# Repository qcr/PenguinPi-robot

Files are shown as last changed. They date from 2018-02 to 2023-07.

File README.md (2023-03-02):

PenguinPi Robot
===============

# Synopsis

This site describes an open-source low-cost robot for educational purposes: hardware and software.

PenguinPi robot

The robot is used for teaching mobile robotics, robotic vision within QUT's EGB439 Advanced Robotics unit.

Key features of the robot are:

* low cost, less than AUD 500
* Raspberry Pi 3B computer with a color camera
* an i/o board with embedded processor that interfaces with motors and provides a simple UI (20x4 OLED display, 4xpushbuttons and various other LEDs)
* a MATLAB-based API, MATLAB code running on a host computer communicates over WiFi with a server running on the robot
* ability to run code onboard written in Python or C++

Example of MATLAB API usage:
```matlab
robot = PiBot('192.168.3.4')
robot.setVelocity(20, -20); % set left & right wheel speeds to +20 and -20 respectively
robot.stop(); % stop the robot moving
batteryVoltage = pb.getVoltage(); % get battery voltage
pb.setLed(2, true);  % turn on the green LED
pb.printfOLED('hello world'); % write string to the OLED display
im = pb.getImage(); % get RGB image from the camera
```

PenguinPi robot

# Mechanical design

The robot has two independently controllable wheels driven by geared DC brushmotors, and a single castor.  The frame is built from laser cut acrylic.

An [animation of the assembly](https://youtu.be/HddVRaQIhIY).

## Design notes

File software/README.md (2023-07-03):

# Welcome to EGB439 Advanced Robotics
Included in this repository is the Python, MATLAB and C code used to operate the PenguinPi using the Raspbian Bullseye (64-bit) operating system.

## Folder structure
The main folders are:
  - [python/robot](./python/robot) Python server that runs on the Raspberry Pi and accepts web service requests. There should be no need to touch this for you.
  - [matlab](./matlab) runs on your computer and talks to the Python server running on the robot.
  - [python/client](./python/client) is an unsupported alternative to the MATLAB client.
  - [atmelStudio](./atmelStudio) C code that runs on the Atmel processor (on the i/o board) that connects the Pi to the robot hardware. There should be no need to touch this for you.

## Startup scripts
The scripts that automatically launch on the robot when starting up are:
* [ppweb.py](./python/robot/ppweb.py) - this is the webserver that MATLAB communicates with.
* [GPIOSoftShutdown.py](./python/GPIOSoftShutdown.py) - this allows you to safely shut down the PenguinPi by means of pressing a button.

## Raspberry pi login
* Username: `pi`
* Password: `PenguinPi` - see [instruction to change](https://www.raspberrypi.com/documentation/computers/configuration.html#change-the-default-password)
* You may want to [change your hostname](https://www.howtogeek.com/167195/how-to-change-your-raspberry-pi-or-other-linux-devices-hostname/). If you wish to change this please speak to your tutor.

## Connecting to your Pi
### The easy way
The easiest way is to connect via a screen and keyboard/mouse. 

### Via Wifi
You can also connect to the PI over the network using ssh over WiFi or the Ethernet cable. See the [README-WiFi.md](README-WiFi.md).

### Using an ethernet cable
The ethernet port can be used. It will be assigned an IP address from the DHCP server in your network (e.g. of the QUT DHCP server). The IP will be shown on the Pi's screen.

### Internet access for the PenguinPi using the QUT Enterprise Network
If you can connect to your PenguinPi on the QUT network, but cannot access internet, you have to use the IAClient. You can set it up by using `~/InternetAccessClient_Linux_ARM32v71-RaspberryPi_v4.0.250_QUT/IAClientConfigCmd` and entering your username and password. If the domain is empty, please enter `qut.edu.au`. You can then run `~/InternetAccessClient_Linux_ARM32v71-RaspberryPi_v4.0.250_QUT/IAClient` in a terminal and keep it open (or run in the background by appending ` &` after the command).

### Old instructions, please ignore or use with caution
<details><summary>More details, but use with caution!</summary>
If you need the IP address to stay the same, it is highly recommended you don't use a static IP, but try using a hostname. If you still must have a static IP address, do not edit the `/etc/network/interfaces` file. Since Raspian Jessie, you should use the `/etc/dhcpcd.conf` file to set a static IP address; to do so, follow these [instructions](https://raspberrypi.stackexchange.com/questions/37920/how-do-i-set-up-networking-wifi-static-ip-address/74428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) or [these ones](https://www.tomshardware.com/how-to/static-ip-raspberry-pi).

If you want to access the internet over the PenguinPis WiFi hotspot (using the raspberry pi as a WiFi router), you will have to enable IP forwarding. This is already enabled by default.
</details>

## Deploying a PenguinPi
- Flash the HAT: `cd ~/PenguinPi-robot/software/atmelStudio && make` (Steven Bulmer to update instructions)
- Set up the network with the correct MAC for the robot: `cd ~/PenguinPi-robot/software/scripts && sudo sh update_networking_script.sh`
- Reboot the PenguinPi
- Set up the proxy: `cd ~/PenguinPi-robot/software/scripts && sh setup_proxy.sh`
- On your local machine, run the `motortest.m` and `cameratest.m` scripts (MATLAB) or the `test_camera_motors.py` script (Python). Note that you will need to update the IP - for the Python script, simply run `python test_camera_motors.py --ip AAA.BBB.CCC.DDD`.

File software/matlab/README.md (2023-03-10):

# MATLAB interface to PenguinPi

The code here allows you to control the robot and access its camera from the MATLAB environment.  You need to have the file
```PiBot.m``` in the current directory or on your MATLAB path.  The Raspberry Pi needs to be running the Python server code [ppweb.py](../python/robot/ppweb.py) (this happens automatically at startup).

## Establishing a connection
We start by connecting to the remote Raspberry Pi
```
pb = PiBot('192.168.1.141');
```
which requires the IP address of the RPi on the network.  This might be the one assigned by the WiFi access point in the 
lab or a hardwired address 192.168.0.100 for the wired ethernet port. 
The result is an object that is a connector to the remote RPi.

## Obtaining camera images
To obtain an image is simply
```
img = pb.getImageFromCamera();
```
which is an RGB image with uint8 pixel data.  Typically acquiring an images takes 100-200ms.

### IP camera package
To obtain images, you need the [MATLAB Support Package for IP Cameras](https://au.mathworks.com/help/supportpkg/ipcamera/index.html). Typically installation is straightforward - MATLAB will simply ask you to install the package when you try to use the `ipcam()` function and you do not have the support package installed. In case you get errors that "There was a problem downloading the support package", please use the [Download Support Packages](https://au.mathworks.com/support/install/support-software-downloader.html) application on a different machine and follow the instructions.

## Motor control
### Access the motor encoders
```
ticks = pb.getMotorTicks();
```
which returns a 2-vector containing the integer tick counts for motor A and motor B.  These are in units of degrees of wheel rotation and wrap around at 2^15/2.1333

### Set the speed
```
pb.setMotorSpeeds(-50,-50);
```
where the two arguments are the speed of motor A and B respectively.  WHAT ARE THE UNITS HERE?

### Stop motors
```
pb.setMotorSpeeds(0,0);
```

## LED control
The PenguinPi board has a 2-digit 7-segment display. You can write a hex number (0-255) to that by
```
pb.setDisplayValue(32);
```
which will display as 20 in hex.  You can change the display base to unsigned decimal by
```
pb.setDisplayMode('u');
```
and now the display will show 32 in decimal.  The decimal point is lit to indicate decimal mode.
Unsigned decimal numbers are in the range (0-99).
There is also a signed decimal display mode for numbers in the range (-9 to +9)
```
pb.setDisplayMode('d');
```

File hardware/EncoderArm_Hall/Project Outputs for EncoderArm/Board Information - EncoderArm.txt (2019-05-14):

Board Information Report
Filename     : T:\Techs\Steve\Projects\170327 - PenguinPi_v2\PCB\EncoderArm_Hall\EncoderArm.PcbDoc
Date         : 8/10/2018
Time         : 12:12:14 PM
Time Elapsed : 00:00:00

General
    Board Size, 1290milsx2525mils
    Components on board, 11
count : 2

Routing Information
    Routing completion, 100.00%
    Connections, 20
    Connections routed, 20
    Connections remaining, 0
count : 4

Layer, Arcs, Pads, Vias, Tracks, Texts, Fills, Regions, ComponentBodies
    Top Layer, 0, 10, 0, 44, 0, 0, 0, 0
    Bottom Layer, 0, 10, 0, 42, 0, 0, 0, 0
    Mechanical 1, 8, 0, 0, 8, 0, 0, 0, 0
    Mechanical 13, 0, 0, 0, 24, 0, 0, 0, 6
    Mechanical 15, 0, 0, 0, 36, 0, 0, 0, 0
    Multi-Layer, 0, 9, 8, 0, 0, 0, 1, 0
    Top Paste, 0, 0, 0, 0, 0, 0, 0, 0
    Top Overlay, 3, 0, 0, 2720, 20, 0, 0, 0
    Top Solder, 0, 0, 0, 0, 0, 0, 0, 0
    Bottom Solder, 0, 0, 0, 0, 0, 0, 0, 0
    Bottom Overlay, 3, 0, 0, 2715, 11, 0, 0, 0
    Bottom Paste, 0, 0, 0, 0, 0, 0, 0, 0
    Drill Guide, 0, 0, 0, 0, 0, 0, 0, 0
    Keep-Out Layer, 0, 0, 0, 0, 0, 0, 0, 0
    Drill Drawing, 0, 0, 0, 0, 0, 0, 0, 0
count : 15

Drill Pairs, Vias
    Top Layer - Bottom Layer, 8
count : 1

Non-Plated Hole Size, Pads, Vias
count : 0

Plated Hole Size, Pads, Vias
    0mils, 20, 0
    20mils, 0, 8
    35.433mils, 6, 0
    78.74mils, 1, 0
    78.74mils, 1, 0
    196.85mils, 1, 0
count : 6

Non-Plated Slot Size / Length, Pads
count : 0

Plated Slot Size / Length, Pads
count : 0

Non-Plated Square Hole Size, Pads
count : 0

Plated Square Hole Size, Pads
count : 0

Top Layer Annular Ring Size, Count
    0mils, 3
    20mils, 8
    23.622mils, 6
count : 3

Mid Layer Annular Ring Size, Count
    0mils, 3
    20mils, 8
    23.622mils, 6
count : 3

Bottom Layer Annular Ring Size, Count
    0mils, 3
    20mils, 8
    23.622mils, 6
count : 3

Pad Solder Mask, Count
    4mils, 29
count : 1

Pad Paste Mask, Count
    0mils, 29
count : 1

Pad Pwr/Gnd Expansion, Count
    20mils, 29
count : 1

Pad Relief Conductor Width, Count
    10mils, 29
count : 1

Pad Relief Air Gap, Count
    10mils, 29
count : 1

Pad Relief Entries, Count
    4, 29
count : 1

Via Solder Mask, Count
    4mils, 8
count : 1

Via Pwr/Gnd Expansion, Count
    20mils, 8
count : 1

Track Width, Count
    0.2mils, 5412
    1.969mils, 16
    3.937mils, 44
    7.874mils, 23
    10mils, 79
    30mils, 15
count : 6

Arc Line Width, Count
    9.843mils, 4
    10mils, 10
count : 2

Arc Radius, Count
    4.921mils, 4
    100mils, 7
    190mils, 1
    275.591mils, 2
count : 4

Arc Degrees, Count
    45, 2
    90, 5
    180, 1
    360, 6
count : 4

Text Height, Count
    40mils, 13
    50mils, 4
    60mils, 14
count : 3

Text Width, Count
    8mils, 4
    10mils, 27
count : 2

Net Track Width, Count
    10mils, 6
count : 1

Net Via Size, Count
    50mils, 6
count : 1

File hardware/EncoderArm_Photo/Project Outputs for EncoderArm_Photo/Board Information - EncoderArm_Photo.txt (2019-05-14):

Board Information Report
Filename     : T:\Techs\Steve\Projects\170327 - PenguinPi_v2\PCB\EncoderArm_Photo\EncoderArm_Photo.PcbDoc
Date         : 9/18/2017
Time         : 12:40:18 PM
Time Elapsed : 00:00:00

General
    Board Size, 1290milsx2525mils
    Components on board, 9
count : 2

Routing Information
    Routing completion, 100.00%
    Connections, 22
    Connections routed, 22
    Connections remaining, 0
count : 4

Layer, Arcs, Pads, Vias, Tracks, Texts, Fills, Regions, ComponentBodies
    Top Layer, 0, 12, 0, 43, 0, 0, 0, 0
    Bottom Layer, 0, 10, 0, 53, 0, 0, 0, 0
    Mechanical 1, 8, 0, 0, 8, 0, 0, 0, 0
    Mechanical 13, 0, 0, 0, 12, 0, 0, 0, 3
    Mechanical 15, 0, 0, 0, 18, 0, 0, 0, 0
    Multi-Layer, 0, 11, 6, 0, 0, 0, 1, 0
    Top Paste, 0, 0, 0, 0, 0, 0, 0, 0
    Top Overlay, 1, 0, 0, 11, 16, 0, 0, 0
    Top Solder, 0, 0, 0, 0, 0, 0, 0, 0
    Bottom Solder, 0, 0, 0, 0, 0, 0, 0, 0
    Bottom Overlay, 1, 0, 0, 1, 6, 0, 0, 0
    Bottom Paste, 0, 0, 0, 0, 0, 0, 0, 0
    Drill Guide, 0, 0, 0, 0, 0, 0, 0, 0
    Keep-Out Layer, 0, 0, 0, 0, 0, 0, 0, 0
    Drill Drawing, 0, 0, 0, 0, 0, 0, 0, 0
count : 15

Drill Pairs, Vias
    Top Layer - Bottom Layer, 6
count : 1

Non-Plated Hole Size, Pads, Vias
count : 0

Plated Hole Size, Pads, Vias
    0mils, 22, 0
    20mils, 0, 6
    35.433mils, 8, 0
    78.74mils, 1, 0
    78.74mils, 1, 0
    196.85mils, 1, 0
count : 6

Non-Plated Slot Size / Length, Pads
count : 0

Plated Slot Size / Length, Pads
count : 0

Non-Plated Square Hole Size, Pads
count : 0

Plated Square Hole Size, Pads
count : 0

Top Layer Annular Ring Size, Count
    0mils, 3
    20mils, 6
    23.622mils, 8
count : 3

Mid Layer Annular Ring Size, Count
    0mils, 3
    20mils, 6
    23.622mils, 8
count : 3

Bottom Layer Annular Ring Size, Count
    0mils, 3
    20mils, 6
    23.622mils, 8
count : 3

Pad Solder Mask, Count
    4mils, 33
count : 1

Pad Paste Mask, Count
    0mils, 33
count : 1

Pad Pwr/Gnd Expansion, Count
    20mils, 33
count : 1

Pad Relief Conductor Width, Count
    10mils, 33
count : 1

Pad Relief Air Gap, Count
    10mils, 33
count : 1

Pad Relief Entries, Count
    4, 33
count : 1

Via Solder Mask, Count
    4mils, 6
count : 1

Via Pwr/Gnd Expansion, Count
    20mils, 6
count : 1

Track Width, Count
    3.937mils, 30
    7.874mils, 12
    10mils, 95
    30mils, 9
count : 4

Arc Line Width, Count
    10mils, 10
count : 1

Arc Radius, Count
    50mils, 1
    100mils, 6
    190mils, 1
    275.591mils, 2
count : 4

Arc Degrees, Count
    45, 2
    90, 5
    180, 1
    360, 2
count : 4

Text Height, Count
    40mils, 3
    50mils, 8
    60mils, 11
count : 3

Text Width, Count
    8mils, 4
    10mils, 18
count : 2

Net Track Width, Count
    10mils, 8
count : 1

Net Via Size, Count
    50mils, 8
count : 1

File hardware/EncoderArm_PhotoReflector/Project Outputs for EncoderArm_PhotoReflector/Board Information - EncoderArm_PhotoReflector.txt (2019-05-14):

Board Information Report
Filename     : T:\Techs\Steve\Projects\170327 - PenguinPi_v2\PCB\EncoderArm_PhotoReflector\EncoderArm_PhotoReflector.PcbDoc
Date         : 9/18/2017
Time         : 2:05:08 PM
Time Elapsed : 00:00:00

General
    Board Size, 1290milsx2525mils
    Components on board, 9
count : 2

Routing Information
    Routing completion, 100.00%
    Connections, 22
    Connections routed, 22
    Connections remaining, 0
count : 4

Layer, Arcs, Pads, Vias, Tracks, Texts, Fills, Regions, ComponentBodies
    Top Layer, 0, 12, 0, 55, 0, 0, 0, 0
    Bottom Layer, 0, 10, 0, 44, 0, 0, 0, 0
    Mechanical 1, 8, 0, 0, 8, 0, 0, 0, 0
    Mechanical 13, 0, 0, 0, 12, 0, 0, 0, 3
    Mechanical 15, 0, 0, 0, 18, 0, 0, 0, 0
    Multi-Layer, 0, 11, 7, 0, 0, 0, 1, 0
    Top Paste, 0, 0, 0, 0, 0, 0, 0, 0
    Top Overlay, 1, 0, 0, 11, 16, 0, 0, 0
    Top Solder, 0, 0, 0, 0, 0, 0, 0, 0
    Bottom Solder, 0, 0, 0, 0, 0, 0, 0, 0
    Bottom Overlay, 1, 0, 0, 1, 6, 0, 0, 0
    Bottom Paste, 0, 0, 0, 0, 0, 0, 0, 0
    Drill Guide, 0, 0, 0, 0, 0, 0, 0, 0
    Keep-Out Layer, 0, 0, 0, 0, 0, 0, 0, 0
    Drill Drawing, 0, 0, 0, 0, 0, 0, 0, 0
count : 15

Drill Pairs, Vias
    Top Layer - Bottom Layer, 7
count : 1

Non-Plated Hole Size, Pads, Vias
count : 0

Plated Hole Size, Pads, Vias
    0mils, 22, 0
    15mils, 0, 7
    35.433mils, 8, 0
    78.74mils, 1, 0
    78.74mils, 1, 0
    196.85mils, 1, 0
count : 6

Non-Plated Slot Size / Length, Pads
count : 0

Plated Slot Size / Length, Pads
count : 0

Non-Plated Square Hole Size, Pads
count : 0

Plated Square Hole Size, Pads
count : 0

Top Layer Annular Ring Size, Count
    0mils, 3
    15mils, 7
    23.622mils, 8
count : 3

Mid Layer Annular Ring Size, Count
    0mils, 3
    15mils, 7
    23.622mils, 8
count : 3

Bottom Layer Annular Ring Size, Count
    0mils, 3
    15mils, 7
    23.622mils, 8
count : 3

Pad Solder Mask, Count
    4mils, 33
count : 1

Pad Paste Mask, Count
    0mils, 33
count : 1

Pad Pwr/Gnd Expansion, Count
    20mils, 33
count : 1

Pad Relief Conductor Width, Count
    10mils, 33
count : 1

Pad Relief Air Gap, Count
    10mils, 33
count : 1

Pad Relief Entries, Count
    4, 33
count : 1

Via Solder Mask, Count
    4mils, 7
count : 1

Via Pwr/Gnd Expansion, Count
    20mils, 7
count : 1

Track Width, Count
    3.937mils, 30
    7.874mils, 12
    10mils, 98
    30mils, 9
count : 4

Arc Line Width, Count
    10mils, 10
count : 1

Arc Radius, Count
    50mils, 1
    100mils, 6
    190mils, 1
    275.591mils, 2
count : 4

Arc Degrees, Count
    45, 2
    90, 5
    180, 1
    360, 2
count : 4

Text Height, Count
    40mils, 7
    50mils, 4
    60mils, 11
count : 3

Text Width, Count
    8mils, 4
    10mils, 18
count : 2

Net Track Width, Count
    10mils, 8
count : 1

Net Via Size, Count
    50mils, 8
count : 1

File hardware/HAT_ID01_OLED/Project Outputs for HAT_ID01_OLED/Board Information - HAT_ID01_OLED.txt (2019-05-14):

Board Information Report
Filename     : T:\Techs\Steve\Projects\170327 - PenguinPi_v2\PCB\HAT_ID01_OLED\HAT_ID01_OLED.PcbDoc
Date         : 11/27/2017
Time         : 12:06:49 PM
Time Elapsed : 00:00:00

General
    Board Size, 2559.11milsx2204.724mils
    Components on board, 57
count : 2

Routing Information
    Routing completion, 100.00%
    Connections, 144
    Connections routed, 144
    Connections remaining, 0
count : 4

Layer, Arcs, Pads, Vias, Tracks, Texts, Fills, Regions, ComponentBodies
    Top Layer, 0, 74, 0, 116, 0, 0, 3, 0
    Bottom Layer, 0, 114, 0, 279, 0, 0, 12, 0
    Mechanical 1, 8, 0, 0, 10, 0, 0, 0, 0
    Mechanical 13, 0, 0, 0, 100, 0, 0, 0, 52
    Mechanical 15, 2, 0, 0, 476, 0, 0, 0, 0
    Multi-Layer, 0, 24, 39, 0, 0, 0, 1, 0
    Top Paste, 0, 0, 0, 0, 0, 0, 0, 0
    Top Overlay, 4, 0, 0, 5436, 69, 0, 0, 0
    Top Solder, 0, 0, 0, 0, 0, 0, 0, 0
    Bottom Solder, 0, 0, 0, 0, 0, 0, 0, 0
    Bottom Overlay, 8, 0, 0, 92, 46, 0, 0, 0
    Bottom Paste, 0, 0, 0, 0, 0, 0, 0, 0
    Drill Guide, 0, 0, 0, 0, 0, 0, 0, 0
    Keep-Out Layer, 8, 0, 0, 10, 0, 0, 0, 0
    Drill Drawing, 0, 0, 0, 0, 0, 0, 0, 0
count : 15

Drill Pairs, Vias
    Top Layer - Bottom Layer, 39
count : 1

Non-Plated Hole Size, Pads, Vias
    118.11mils, 4, 0
count : 1

Plated Hole Size, Pads, Vias
    0mils, 188, 0
    20mils, 0, 37
    28mils, 0, 2
    30mils, 4, 0
    35.433mils, 16, 0
count : 5

Non-Plated Slot Size / Length, Pads
count : 0

Plated Slot Size / Length, Pads
count : 0

Non-Plated Square Hole Size, Pads
count : 0

Plated Square Hole Size, Pads
count : 0

Top Layer Annular Ring Size, Count
    0mils, 4
    10mils, 7
    20mils, 30
    22mils, 2
    23.622mils, 16
    30mils, 4
count : 6

Mid Layer Annular Ring Size, Count
    0mils, 4
    10mils, 7
    20mils, 30
    22mils, 2
    23.622mils, 16
    30mils, 4
count : 6

Bottom Layer Annular Ring Size, Count
    0mils, 4
    10mils, 7
    20mils, 30
    22mils, 2
    23.622mils, 16
    30mils, 4
count : 6

Pad Solder Mask, Count
    4mils, 208
    62.992mils, 4
count : 2

Pad Paste Mask, Count
    0mils, 212
count : 1

Pad Pwr/Gnd Expansion, Count
    20mils, 212
count : 1

Pad Relief Conductor Width, Count
    10mils, 212
count : 1

Pad Relief Air Gap, Count
    10mils, 212
count : 1

Pad Relief Entries, Count
    4, 212
count : 1

Via Solder Mask, Count
    4mils, 39
count : 1

Via Pwr/Gnd Expansion, Count
    20mils, 39
count : 1

Track Width, Count
    0.2mils, 5412
    1.969mils, 92
    3.937mils, 568
    7.874mils, 12
    10mils, 430
    20mils, 5
count : 6

Arc Line Width, Count
    3.937mils, 6
    9.843mils, 2
    10mils, 20
    23.622mils, 2
count : 4

Arc Radius, Count
    1.969mils, 4
    3.937mils, 4
    4.921mils, 2
    11.811mils, 2
    19.685mils, 2
    118.11mils, 16
count : 6

Arc Degrees, Count
    90, 16
    360, 14
count : 2

Text Height, Count
    40mils, 22
    50mils, 66
    60mils, 27
count : 3

Text Width, Count
    10mils, 115
count : 1

Net Track Width, Count
    10mils, 64
count : 1

Net Via Size, Count
    50mils, 64
count : 1

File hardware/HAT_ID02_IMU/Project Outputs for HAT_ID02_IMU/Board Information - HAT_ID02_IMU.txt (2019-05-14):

Board Information Report
Filename     : T:\Techs\Steve\Projects\170327 - PenguinPi_v2\PCB\HAT_ID02_IMU\HAT_ID02_IMU.PcbDoc
Date         : 4/16/2018
Time         : 1:02:32 PM
Time Elapsed : 00:00:00

General
    Board Size, 2559.11milsx2204.724mils
    Components on board, 30
count : 2

Routing Information
    Routing completion, 100.00%
    Connections, 98
    Connections routed, 98
    Connections remaining, 0
count : 4

Layer, Arcs, Pads, Vias, Tracks, Texts, Fills, Regions, ComponentBodies
    Top Layer, 0, 53, 0, 106, 0, 0, 4, 0
    Bottom Layer, 0, 56, 0, 146, 0, 0, 7, 0
    Mechanical 1, 8, 0, 0, 10, 0, 0, 0, 0
    Mechanical 13, 1, 0, 0, 20, 0, 0, 0, 24
    Mechanical 15, 1, 0, 0, 180, 0, 0, 0, 0
    Multi-Layer, 0, 35, 22, 0, 0, 0, 1, 0
    Top Paste, 0, 0, 0, 0, 0, 0, 0, 0
    Top Overlay, 7, 0, 0, 5460, 30, 0, 0, 0
    Top Solder, 0, 0, 0, 0, 0, 0, 0, 0
    Bottom Solder, 0, 0, 0, 0, 0, 0, 0, 0
    Bottom Overlay, 2, 0, 0, 60, 34, 0, 0, 0
    Bottom Paste, 0, 0, 0, 0, 0, 0, 0, 0
    Drill Guide, 0, 0, 0, 0, 0, 0, 0, 0
    Keep-Out Layer, 8, 0, 0, 10, 0, 0, 0, 0
    Drill Drawing, 0, 0, 0, 0, 0, 0, 0, 0
count : 15

Drill Pairs, Vias
    Top Layer - Bottom Layer, 22
count : 1

Non-Plated Hole Size, Pads, Vias
    118.11mils, 4, 0
count : 1

Plated Hole Size, Pads, Vias
    0mils, 109, 0
    15mils, 0, 6
    20mils, 0, 16
    30mils, 15, 0
    35.433mils, 16, 0
count : 5

Non-Plated Slot Size / Length, Pads
count : 0

Plated Slot Size / Length, Pads
count : 0

Non-Plated Square Hole Size, Pads
count : 0

Plated Square Hole Size, Pads
count : 0

Top Layer Annular Ring Size, Count
    0mils, 4
    10mils, 13
    20mils, 9
    23.622mils, 16
    30mils, 15
count : 5

Mid Layer Annular Ring Size, Count
    0mils, 4
    10mils, 13
    20mils, 9
    23.622mils, 16
    30mils, 15
count : 5

Bottom Layer Annular Ring Size, Count
    0mils, 4
    10mils, 13
    20mils, 9
    23.622mils, 16
    30mils, 15
count : 5

Pad Solder Mask, Count
    4mils, 140
    62.992mils, 4
count : 2

Pad Paste Mask, Count
    0mils, 144
count : 1

Pad Pwr/Gnd Expansion, Count
    20mils, 144
count : 1

Pad Relief Conductor Width, Count
    10mils, 144
count : 1

Pad Relief Air Gap, Count
    10mils, 144
count : 1

Pad Relief Entries, Count
    4, 144
count : 1

Via Solder Mask, Count
    4mils, 22
count : 1

Via Pwr/Gnd Expansion, Count
    20mils, 22
count : 1

Track Width, Count
    0.2mils, 5412
    1.969mils, 64
    3.937mils, 192
    7.874mils, 16
    10mils, 308
count : 5

Arc Line Width, Count
    3.937mils, 2
    9.843mils, 2
    10mils, 21
    15mils, 1
    23.622mils, 1
count : 5

Arc Radius, Count
    3.937mils, 4
    4.921mils, 2
    7mils, 1
    11.811mils, 1
    19.685mils, 2
    41.231mils, 1
    118.11mils, 16
count : 7

Arc Degrees, Count
    90, 16
    360, 11
count : 2

Text Height, Count
    40mils, 23
    50mils, 24
    60mils, 17
count : 3

Text Width, Count
    10mils, 64
count : 1

Net Track Width, Count
    8mils, 28
count : 1

Net Via Size, Count
    50mils, 28
count : 1

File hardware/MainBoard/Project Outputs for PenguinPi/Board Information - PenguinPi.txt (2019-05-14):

Board Information Report
Filename     : T:\Techs\Steve\Projects\170327 - PenguinPi_v2\PCB\MainBoard\PenguinPi.PcbDoc
Date         : 12/1/2017
Time         : 10:59:30 AM
Time Elapsed : 00:00:00

General
    Board Size, 2559.11milsx3103.936mils
    Components on board, 57
count : 2

Routing Information
    Routing completion, 100.00%
    Connections, 172
    Connections routed, 172
    Connections remaining, 0
count : 4

Layer, Arcs, Pads, Vias, Tracks, Texts, Fills, Regions, ComponentBodies
    Top Layer, 0, 112, 0, 369, 0, 0, 25, 0
    Bottom Layer, 0, 48, 0, 311, 0, 0, 23, 0
    Mechanical 1, 9, 0, 0, 10, 0, 0, 0, 0
    Mechanical 13, 1, 0, 0, 20, 0, 0, 0, 40
    Mechanical 15, 0, 0, 0, 320, 0, 0, 0, 0
    Multi-Layer, 0, 103, 88, 0, 0, 0, 1, 0
    Top Paste, 0, 0, 0, 0, 0, 0, 0, 0
    Top Overlay, 12, 0, 0, 5541, 85, 0, 0, 0
    Top Solder, 0, 0, 0, 0, 0, 0, 0, 0
    Bottom Solder, 0, 0, 0, 0, 0, 0, 0, 0
    Bottom Overlay, 2, 0, 0, 82, 44, 0, 0, 0
    Bottom Paste, 0, 0, 0, 0, 0, 0, 0, 0
    Drill Guide, 0, 0, 0, 0, 0, 0, 0, 0
    Keep-Out Layer, 12, 0, 0, 10, 0, 0, 0, 0
    Drill Drawing, 0, 0, 0, 0, 0, 0, 0, 0
count : 15

Drill Pairs, Vias
    Top Layer - Bottom Layer, 88
count : 1

Non-Plated Hole Size, Pads, Vias
    118.11mils, 4, 0
count : 1

Plated Hole Size, Pads, Vias
    0mils, 160, 0
    10mils, 0, 26
    15mils, 0, 59
    28mils, 0, 3
    35.433mils, 28, 0
    40mils, 60, 0
    47.244mils, 2, 0
    55.118mils, 2, 0
    59.055mils, 5, 0
    74.803mils, 2, 0
count : 10

Non-Plated Slot Size / Length, Pads
count : 0

Plated Slot Size / Length, Pads
count : 0

Non-Plated Square Hole Size, Pads
count : 0

Plated Square Hole Size, Pads
count : 0

Top Layer Annular Ring Size, Count
    0mils, 6
    5mils, 26
    15mils, 59
    19.685mils, 5
    22mils, 3
    23.622mils, 28
    30mils, 60
    31.496mils, 2
    43.307mils, 2
count : 9

Mid Layer Annular Ring Size, Count
    0mils, 6
    5mils, 26
    15mils, 59
    19.685mils, 5
    22mils, 3
    23.622mils, 28
    30mils, 60
    31.496mils, 2
    43.307mils, 2
count : 9

Bottom Layer Annular Ring Size, Count
    0mils, 6
    5mils, 26
    15mils, 59
    19.685mils, 5
    22mils, 3
    23.622mils, 28
    30mils, 60
    31.496mils, 2
    43.307mils, 2
count : 9

Pad Solder Mask, Count
    0mils, 2
    4mils, 257
    62.992mils, 4
count : 3

Pad Paste Mask, Count
    0mils, 263
count : 1

Pad Pwr/Gnd Expansion, Count
    20mils, 263
count : 1

Pad Relief Conductor Width, Count
    10mils, 263
count : 1

Pad Relief Air Gap, Count
    10mils, 263
count : 1

Pad Relief Entries, Count
    4, 263
count : 1

Via Solder Mask, Count
    4mils, 88
count : 1

Via Pwr/Gnd Expansion, Count
    20mils, 88
count : 1

Track Width, Count
    0.2mils, 5412
    1.969mils, 128
    3.937mils, 324
    7.874mils, 31
    10mils, 666
    20mils, 12
    30mils, 90
count : 7

Arc Line Width, Count
    3.937mils, 2
    9.843mils, 3
    10mils, 30
    23.622mils, 1
count : 4

Arc Radius, Count
    1.969mils, 1
    3.937mils, 2
    4.921mils, 3
    5mils, 2
    11.811mils, 1
    19.685mils, 1
    39.37mils, 2
    39.37mils, 8
    78.74mils, 5
    118.11mils, 8
    118.11mils, 1
    118.176mils, 2
count : 12

Arc Degrees, Count
    90, 16
    172, 5
    180, 2
    360, 13
count : 4

Text Height, Count
    40mils, 60
    50mils, 23
    60mils, 46
count : 3

Text Width, Count
    8mils, 12
    10mils, 117
count : 2

Net Track Width, Count
    10mils, 63
count : 1

Net Via Size, Count
    50mils, 63
count : 1

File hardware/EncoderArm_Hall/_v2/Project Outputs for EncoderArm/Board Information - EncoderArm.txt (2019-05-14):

Board Information Report
Filename     : T:\Techs\Steve\Projects\170327 - PenguinPi_v2\PCB\EncoderArm_Hall\EncoderArm.PcbDoc
Date         : 10/27/2017
Time         : 9:07:12 AM
Time Elapsed : 00:00:00

General
    Board Size, 1290milsx2525mils
    Components on board, 11
count : 2

Routing Information
    Routing completion, 100.00%
    Connections, 20
    Connections routed, 20
    Connections remaining, 0
count : 4

Layer, Arcs, Pads, Vias, Tracks, Texts, Fills, Regions, ComponentBodies
    Top Layer, 0, 10, 0, 43, 0, 0, 0, 0
    Bottom Layer, 0, 10, 0, 43, 0, 0, 0, 0
    Mechanical 1, 8, 0, 0, 8, 0, 0, 0, 0
    Mechanical 13, 0, 0, 0, 24, 0, 0, 0, 6
    Mechanical 15, 0, 0, 0, 36, 0, 0, 0, 0
    Multi-Layer, 0, 9, 8, 0, 0, 0, 1, 0
    Top Paste, 0, 0, 0, 0, 0, 0, 0, 0
    Top Overlay, 3, 0, 0, 2720, 19, 0, 0, 0
    Top Solder, 0, 0, 0, 0, 0, 0, 0, 0
    Bottom Solder, 0, 0, 0, 0, 0, 0, 0, 0
    Bottom Overlay, 3, 0, 0, 2715, 10, 0, 0, 0
    Bottom Paste, 0, 0, 0, 0, 0, 0, 0, 0
    Drill Guide, 0, 0, 0, 0, 0, 0, 0, 0
    Keep-Out Layer, 0, 0, 0, 0, 0, 0, 0, 0
    Drill Drawing, 0, 0, 0, 0, 0, 0, 0, 0
count : 15

Drill Pairs, Vias
    Top Layer - Bottom Layer, 8
count : 1

Non-Plated Hole Size, Pads, Vias
count : 0

Plated Hole Size, Pads, Vias
    0mils, 20, 0
    20mils, 0, 8
    35.433mils, 6, 0
    78.74mils, 1, 0
    78.74mils, 1, 0
    196.85mils, 1, 0
count : 6

Non-Plated Slot Size / Length, Pads
count : 0

Plated Slot Size / Length, Pads
count : 0

Non-Plated Square Hole Size, Pads
count : 0

Plated Square Hole Size, Pads
count : 0

Top Layer Annular Ring Size, Count
    0mils, 3
    20mils, 8
    23.622mils, 6
count : 3

Mid Layer Annular Ring Size, Count
    0mils, 3
    20mils, 8
    23.622mils, 6
count : 3

Bottom Layer Annular Ring Size, Count
    0mils, 3
    20mils, 8
    23.622mils, 6
count : 3

Pad Solder Mask, Count
    4mils, 29
count : 1

Pad Paste Mask, Count
    0mils, 29
count : 1

Pad Pwr/Gnd Expansion, Count
    20mils, 29
count : 1

Pad Relief Conductor Width, Count
    10mils, 29
count : 1

Pad Relief Air Gap, Count
    10mils, 29
count : 1

Pad Relief Entries, Count
    4, 29
count : 1

Via Solder Mask, Count
    4mils, 8
count : 1

Via Pwr/Gnd Expansion, Count
    20mils, 8
count : 1

Track Width, Count
    0.2mils, 5412
    1.969mils, 16
    3.937mils, 44
    7.874mils, 23
    10mils, 79
    30mils, 15
count : 6

Arc Line Width, Count
    9.843mils, 4
    10mils, 10
count : 2

Arc Radius, Count
    4.921mils, 4
    100mils, 7
    190mils, 1
    275.591mils, 2
count : 4

Arc Degrees, Count
    45, 2
    90, 5
    180, 1
    360, 6
count : 4

Text Height, Count
    40mils, 11
    50mils, 4
    60mils, 14
count : 3

Text Width, Count
    8mils, 4
    10mils, 25
count : 2

Net Track Width, Count
    10mils, 6
count : 1

Net Via Size, Count
    50mils, 6
count : 1

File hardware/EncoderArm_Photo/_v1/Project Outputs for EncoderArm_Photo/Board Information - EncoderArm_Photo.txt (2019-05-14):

Board Information Report
Filename     : T:\Techs\Steve\Projects\170327 - PenguinPi_v2\PCB\EncoderArm_Photo\EncoderArm_Photo.PcbDoc
Date         : 8/15/2017
Time         : 11:47:31 PM
Time Elapsed : 00:00:00

General
    Board Size, 1360milsx2525mils
    Components on board, 9
count : 2

Routing Information
    Routing completion, 100.00%
    Connections, 22
    Connections routed, 22
    Connections remaining, 0
count : 4

Layer, Arcs, Pads, Vias, Tracks, Texts, Fills, Regions, ComponentBodies
    Top Layer, 0, 12, 0, 43, 0, 0, 0, 0
    Bottom Layer, 0, 10, 0, 52, 0, 0, 0, 0
    Mechanical 1, 8, 0, 0, 8, 0, 0, 0, 0
    Mechanical 13, 0, 0, 0, 12, 0, 0, 0, 3
    Mechanical 15, 0, 0, 0, 18, 0, 0, 0, 0
    Multi-Layer, 0, 11, 6, 0, 0, 0, 1, 0
    Top Paste, 0, 0, 0, 0, 0, 0, 0, 0
    Top Overlay, 1, 0, 0, 11, 16, 0, 0, 0
    Top Solder, 0, 0, 0, 0, 0, 0, 0, 0
    Bottom Solder, 0, 0, 0, 0, 0, 0, 0, 0
    Bottom Overlay, 1, 0, 0, 1, 6, 0, 0, 0
    Bottom Paste, 0, 0, 0, 0, 0, 0, 0, 0
    Drill Guide, 0, 0, 0, 0, 0, 0, 0, 0
    Keep-Out Layer, 0, 0, 0, 0, 0, 0, 0, 0
    Drill Drawing, 0, 0, 0, 0, 0, 0, 0, 0
count : 15

Drill Pairs, Vias
    Top Layer - Bottom Layer, 6
count : 1

Non-Plated Hole Size, Pads, Vias
count : 0

Plated Hole Size, Pads, Vias
    0mils, 22, 0
    20mils, 0, 6
    35.433mils, 8, 0
    78.74mils, 1, 0
    78.74mils, 1, 0
    196.85mils, 1, 0
count : 6

Non-Plated Slot Size / Length, Pads
count : 0

Plated Slot Size / Length, Pads
count : 0

Non-Plated Square Hole Size, Pads
count : 0

Plated Square Hole Size, Pads
count : 0

Top Layer Annular Ring Size, Count
    0mils, 3
    20mils, 6
    23.622mils, 8
count : 3

Mid Layer Annular Ring Size, Count
    0mils, 3
    20mils, 6
    23.622mils, 8
count : 3

Bottom Layer Annular Ring Size, Count
    0mils, 3
    20mils, 6
    23.622mils, 8
count : 3

Pad Solder Mask, Count
    4mils, 33
count : 1

Pad Paste Mask, Count
    0mils, 33
count : 1

Pad Pwr/Gnd Expansion, Count
    20mils, 33
count : 1

Pad Relief Conductor Width, Count
    10mils, 33
count : 1

Pad Relief Air Gap, Count
    10mils, 33
count : 1

Pad Relief Entries, Count
    4, 33
count : 1

Via Solder Mask, Count
    4mils, 6
count : 1

Via Pwr/Gnd Expansion, Count
    20mils, 6
count : 1

Track Width, Count
    3.937mils, 30
    7.874mils, 12
    10mils, 94
    30mils, 9
count : 4

Arc Line Width, Count
    10mils, 10
count : 1

Arc Radius, Count
    50mils, 1
    100mils, 6
    150mils, 1
    275.591mils, 2
count : 4

Arc Degrees, Count
    45, 2
    90, 5
    180, 1
    360, 2
count : 4

Text Height, Count
    40mils, 2
    50mils, 9
    60mils, 11
count : 3

Text Width, Count
    8mils, 4
    10mils, 18
count : 2

Net Track Width, Count
    10mils, 8
count : 1

Net Via Size, Count
    50mils, 8
count : 1

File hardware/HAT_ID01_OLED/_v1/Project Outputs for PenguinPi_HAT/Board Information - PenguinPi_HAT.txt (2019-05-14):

Board Information Report
Filename     : T:\Techs\Steve\Projects\170327 - PenguinPi_v2\PCB\MainBoard\PenguinPi_HAT.PcbDoc
Date         : 8/15/2017
Time         : 4:43:27 PM
Time Elapsed : 00:00:00

General
    Board Size, 2559.11milsx2204.724mils
    Components on board, 43
count : 2

Routing Information
    Routing completion, 100.00%
    Connections, 116
    Connections routed, 116
    Connections remaining, 0
count : 4

Layer, Arcs, Pads, Vias, Tracks, Texts, Fills, Regions, ComponentBodies
    Top Layer, 0, 56, 0, 94, 0, 0, 2, 0
    Bottom Layer, 0, 104, 0, 253, 0, 0, 14, 0
    Mechanical 1, 8, 0, 0, 10, 0, 0, 0, 0
    Mechanical 13, 0, 0, 0, 64, 0, 0, 0, 38
    Mechanical 15, 2, 0, 0, 372, 0, 0, 0, 0
    Multi-Layer, 0, 24, 32, 0, 0, 0, 1, 0
    Top Paste, 0, 0, 0, 0, 0, 0, 0, 0
    Top Overlay, 4, 0, 0, 5436, 51, 0, 0, 0
    Top Solder, 0, 0, 0, 0, 0, 0, 0, 0
    Bottom Solder, 0, 0, 0, 0, 0, 0, 0, 0
    Bottom Overlay, 8, 0, 0, 72, 36, 0, 0, 0
    Bottom Paste, 0, 0, 0, 0, 0, 0, 0, 0
    Drill Guide, 0, 0, 0, 0, 0, 0, 0, 0
    Keep-Out Layer, 8, 0, 0, 10, 0, 0, 0, 0
    Drill Drawing, 0, 0, 0, 0, 0, 0, 0, 0
count : 15

Drill Pairs, Vias
    Top Layer - Bottom Layer, 32
count : 1

Non-Plated Hole Size, Pads, Vias
    118.11mils, 4, 0
count : 1

Plated Hole Size, Pads, Vias
    0mils, 160, 0
    20mils, 0, 30
    28mils, 0, 2
    30mils, 4, 0
    35.433mils, 16, 0
count : 5

Non-Plated Slot Size / Length, Pads
count : 0

Plated Slot Size / Length, Pads
count : 0

Non-Plated Square Hole Size, Pads
count : 0

Plated Square Hole Size, Pads
count : 0

Top Layer Annular Ring Size, Count
    0mils, 4
    10mils, 5
    20mils, 25
    22mils, 2
    23.622mils, 16
    30mils, 4
count : 6

Mid Layer Annular Ring Size, Count
    0mils, 4
    10mils, 5
    20mils, 25
    22mils, 2
    23.622mils, 16
    30mils, 4
count : 6

Bottom Layer Annular Ring Size, Count
    0mils, 4
    10mils, 5
    20mils, 25
    22mils, 2
    23.622mils, 16
    30mils, 4
count : 6

Pad Solder Mask, Count
    4mils, 180
    62.992mils, 4
count : 2

Pad Paste Mask, Count
    0mils, 184
count : 1

Pad Pwr/Gnd Expansion, Count
    20mils, 184
count : 1

Pad Relief Conductor Width, Count
    10mils, 184
count : 1

Pad Relief Air Gap, Count
    10mils, 184
count : 1

Pad Relief Entries, Count
    4, 184
count : 1

Via Solder Mask, Count
    4mils, 32
count : 1

Via Pwr/Gnd Expansion, Count
    20mils, 32
count : 1

Track Width, Count
    0.2mils, 5412
    1.969mils, 72
    3.937mils, 428
    7.874mils, 12
    10mils, 386
    20mils, 1
count : 6

Arc Line Width, Count
    3.937mils, 6
    9.843mils, 2
    10mils, 20
    23.622mils, 2
count : 4

Arc Radius, Count
    1.969mils, 4
    3.937mils, 4
    4.921mils, 2
    11.811mils, 2
    19.685mils, 2
    118.11mils, 16
count : 6

Arc Degrees, Count
    90, 16
    360, 14
count : 2

Text Height, Count
    40mils, 4
    50mils, 69
    60mils, 14
count : 3

Text Width, Count
    10mils, 87
count : 1

Net Track Width, Count
    10mils, 59
count : 1

Net Via Size, Count
    50mils, 59
count : 1

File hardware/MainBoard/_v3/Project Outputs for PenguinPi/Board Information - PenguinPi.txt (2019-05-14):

Board Information Report
Filename     : T:\Techs\Steve\Projects\170327 - PenguinPi_v2\PCB\MainBoard\PenguinPi.PcbDoc
Date         : 11/14/2017
Time         : 1:57:17 PM
Time Elapsed : 00:00:00

General
    Board Size, 2559.11milsx3103.936mils
    Components on board, 57
count : 2

Routing Information
    Routing completion, 100.00%
    Connections, 171
    Connections routed, 171
    Connections remaining, 0
count : 4

Layer, Arcs, Pads, Vias, Tracks, Texts, Fills, Regions, ComponentBodies
    Top Layer, 0, 110, 0, 370, 0, 0, 0, 0
    Bottom Layer, 0, 47, 0, 331, 0, 0, 0, 0
    Mechanical 1, 9, 0, 0, 10, 0, 0, 0, 0
    Mechanical 13, 1, 0, 0, 20, 0, 0, 0, 40
    Mechanical 15, 0, 0, 0, 320, 0, 0, 0, 0
    Multi-Layer, 0, 103, 67, 0, 0, 0, 1, 0
    Top Paste, 0, 0, 0, 0, 0, 0, 0, 0
    Top Overlay, 12, 0, 0, 5543, 87, 0, 0, 0
    Top Solder, 0, 0, 0, 0, 0, 0, 0, 0
    Bottom Solder, 0, 0, 0, 0, 0, 0, 0, 0
    Bottom Overlay, 2, 0, 0, 80, 45, 0, 0, 0
    Bottom Paste, 0, 0, 0, 0, 0, 0, 0, 0
    Drill Guide, 0, 0, 0, 0, 0, 0, 0, 0
    Keep-Out Layer, 12, 0, 0, 10, 0, 0, 0, 0
    Drill Drawing, 0, 0, 0, 0, 0, 0, 0, 0
count : 15

Drill Pairs, Vias
    Top Layer - Bottom Layer, 67
count : 1

Non-Plated Hole Size, Pads, Vias
    118.11mils, 4, 0
count : 1

Plated Hole Size, Pads, Vias
    0mils, 157, 0
    15mils, 0, 62
    28mils, 0, 5
    35.433mils, 28, 0
    40mils, 60, 0
    47.244mils, 2, 0
    59.055mils, 7, 0
    74.803mils, 2, 0
count : 8

Non-Plated Slot Size / Length, Pads
count : 0

Plated Slot Size / Length, Pads
count : 0

Non-Plated Square Hole Size, Pads
count : 0

Plated Square Hole Size, Pads
count : 0

Top Layer Annular Ring Size, Count
    0mils, 4
    15mils, 62
    19.685mils, 5
    22mils, 5
    23.622mils, 28
    30mils, 60
    31.496mils, 2
    39.37mils, 2
    43.307mils, 2
count : 9

Mid Layer Annular Ring Size, Count
    0mils, 4
    15mils, 62
    19.685mils, 5
    22mils, 5
    23.622mils, 28
    30mils, 60
    31.496mils, 2
    39.37mils, 2
    43.307mils, 2
count : 9

Bottom Layer Annular Ring Size, Count
    0mils, 4
    15mils, 62
    19.685mils, 5
    22mils, 5
    23.622mils, 28
    30mils, 60
    31.496mils, 2
    39.37mils, 2
    43.307mils, 2
count : 9

Pad Solder Mask, Count
    0mils, 2
    4mils, 254
    62.992mils, 4
count : 3

Pad Paste Mask, Count
    0mils, 260
count : 1

Pad Pwr/Gnd Expansion, Count
    20mils, 260
count : 1

Pad Relief Conductor Width, Count
    10mils, 260
count : 1

Pad Relief Air Gap, Count
    10mils, 260
count : 1

Pad Relief Entries, Count
    4, 260
count : 1

Via Solder Mask, Count
    4mils, 67
count : 1

Via Pwr/Gnd Expansion, Count
    20mils, 67
count : 1

Track Width, Count
    0.2mils, 5412
    1.969mils, 128
    3.937mils, 324
    7.874mils, 31
    10mils, 671
    20mils, 12
    30mils, 106
count : 7

Arc Line Width, Count
    3.937mils, 2
    9.843mils, 3
    10mils, 30
    23.622mils, 1
count : 4

Arc Radius, Count
    1.969mils, 1
    3.937mils, 2
    4.921mils, 3
    5mils, 2
    11.811mils, 1
    19.685mils, 1
    39.37mils, 2
    39.37mils, 8
    78.74mils, 5
    118.11mils, 8
    118.11mils, 1
    118.176mils, 2
count : 12

Arc Degrees, Count
    90, 16
    172, 5
    180, 2
    360, 13
count : 4

Text Height, Count
    40mils, 60
    50mils, 25
    60mils, 47
count : 3

Text Width, Count
    8mils, 12
    10mils, 120
count : 2

Net Track Width, Count
    10mils, 63
count : 1

Net Via Size, Count
    50mils, 63
count : 1

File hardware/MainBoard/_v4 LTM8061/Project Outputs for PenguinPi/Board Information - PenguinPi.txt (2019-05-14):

Board Information Report
Filename     : T:\Techs\Steve\Projects\170327 - PenguinPi_v2\PCB\MainBoard\PenguinPi.PcbDoc
Date         : 11/27/2017
Time         : 2:03:24 PM
Time Elapsed : 00:00:00

General
    Board Size, 2559.11milsx3103.936mils
    Components on board, 66
count : 2

Routing Information
    Routing completion, 100.00%
    Connections, 256
    Connections routed, 256
    Connections remaining, 0
count : 4

Layer, Arcs, Pads, Vias, Tracks, Texts, Fills, Regions, ComponentBodies
    Top Layer, 0, 201, 0, 419, 0, 6, 28, 0
    Bottom Layer, 0, 52, 0, 331, 0, 0, 24, 0
    Mechanical 1, 9, 0, 0, 10, 0, 0, 0, 0
    Mechanical 13, 1, 0, 0, 32, 0, 0, 0, 49
    Mechanical 15, 0, 0, 0, 398, 0, 0, 0, 0
    Multi-Layer, 0, 103, 120, 0, 0, 0, 1, 0
    Top Paste, 0, 0, 0, 0, 0, 0, 0, 0
    Top Overlay, 14, 0, 0, 5563, 99, 0, 0, 0
    Top Solder, 0, 0, 0, 0, 0, 0, 0, 0
    Bottom Solder, 0, 0, 0, 0, 0, 0, 0, 0
    Bottom Overlay, 2, 0, 0, 90, 48, 0, 0, 0
    Bottom Paste, 0, 0, 0, 0, 0, 0, 0, 0
    Drill Guide, 0, 0, 0, 0, 0, 0, 0, 0
    Keep-Out Layer, 12, 0, 0, 10, 0, 0, 0, 0
    Drill Drawing, 0, 0, 0, 0, 0, 0, 0, 0
count : 15

Drill Pairs, Vias
    Top Layer - Bottom Layer, 120
count : 1

Non-Plated Hole Size, Pads, Vias
    118.11mils, 4, 0
count : 1

Plated Hole Size, Pads, Vias
    0mils, 253, 0
    10mils, 0, 56
    15mils, 0, 61
    28mils, 0, 3
    35.433mils, 28, 0
    40mils, 60, 0
    47.244mils, 2, 0
    55.118mils, 2, 0
    59.055mils, 5, 0
    74.803mils, 2, 0
count : 10

Non-Plated Slot Size / Length, Pads
count : 0

Plated Slot Size / Length, Pads
count : 0

Non-Plated Square Hole Size, Pads
count : 0

Plated Square Hole Size, Pads
count : 0

Top Layer Annular Ring Size, Count
    0mils, 6
    5mils, 56
    15mils, 61
    19.685mils, 5
    22mils, 3
    23.622mils, 28
    30mils, 60
    31.496mils, 2
    43.307mils, 2
count : 9

Mid Layer Annular Ring Size, Count
    0mils, 6
    5mils, 56
    15mils, 61
    19.685mils, 5
    22mils, 3
    23.622mils, 28
    30mils, 60
    31.496mils, 2
    43.307mils, 2
count : 9

Bottom Layer Annular Ring Size, Count
    0mils, 6
    5mils, 56
    15mils, 61
    19.685mils, 5
    22mils, 3
    23.622mils, 28
    30mils, 60
    31.496mils, 2
    43.307mils, 2
count : 9

Pad Solder Mask, Count
    0mils, 79
    4mils, 273
    62.992mils, 4
count : 3

Pad Paste Mask, Count
    0mils, 356
count : 1

Pad Pwr/Gnd Expansion, Count
    20mils, 356
count : 1

Pad Relief Conductor Width, Count
    10mils, 356
count : 1

Pad Relief Air Gap, Count
    10mils, 356
count : 1

Pad Relief Entries, Count
    4, 356
count : 1

Via Solder Mask, Count
    4mils, 120
count : 1

Via Pwr/Gnd Expansion, Count
    20mils, 120
count : 1

Track Width, Count
    0.2mils, 5412
    1.969mils, 156
    3.937mils, 406
    7.874mils, 39
    10mils, 728
    20mils, 12
    30mils, 100
count : 7

Arc Line Width, Count
    3.937mils, 3
    9.843mils, 4
    10mils, 30
    23.622mils, 1
count : 4

Arc Radius, Count
    1.969mils, 2
    3.937mils, 2
    4.921mils, 4
    5mils, 2
    11.811mils, 1
    19.685mils, 1
    39.37mils, 2
    39.37mils, 8
    78.74mils, 5
    118.11mils, 8
    118.11mils, 1
    118.176mils, 2
count : 12

Arc Degrees, Count
    90, 16
    172, 5
    180, 2
    360, 15
count : 4

Text Height, Count
    40mils, 71
    50mils, 23
    60mils, 53
count : 3

Text Width, Count
    8mils, 12
    10mils, 135
count : 2

Net Track Width, Count
    10mils, 70
count : 1

Net Via Size, Count
    50mils, 70
count : 1

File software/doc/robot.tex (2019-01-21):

\documentclass[11pt,fleqn]{article}
\usepackage{geometry} % see geometry.pdf on how to lay out the page. There's lots.
\geometry{a4paper} % or letter or a5paper or ... etc
% \geometry{landscape} % rotated page geometry
\usepackage{enumitem}

% See the ``Article customise'' template for come common customisations
\usepackage{times}
\usepackage{graphicx}
\usepackage{wrapfig}
\usepackage{xcolor}
\usepackage{url}
\usepackage{hyperref}
\usepackage{colortbl}
\usepackage{fancyhdr}
\usepackage{pdfpages}
\usepackage{pdflscape}
\usepackage{longtable}
\usepackage{arydshln}

\include{rvc-notation}

\setlength{\parindent}{0pt}
\newcommand{\IDX}[1]{\textbf{\textcolor{red}{#1}}}
\newcommand{\SIDENOTE}[1]{\textbf{\textcolor{blue}{#1}}}
\newcommand{\rpi}{Raspberry Pi}

\title{A mobile robot for education: the PenguinPi}
\author{Peter Corke}
\date{July 2018} % delete this line to display the current date

\makeatletter
           \let\Date\@date
\makeatother

%%% BEGIN DOCUMENT
\begin{document}
\maketitle
\pagestyle{fancyplain}
%\pagestyle{headings}        % Gives page headings at top of page
\rfoot{Revision of \today }
%\rfoot{Copyright \copyright Peter Corke \rtbyear}

This report describes a low-cost mobile robot  designed for robotics education.
The teaching objectives are described and this leads to a specification for the robot.
The remainder of the report provides a detailed technical description of the Penguin Pi  robot and its implementation.

\begin{figure}[h]
\centering

%\caption{The Mark II Penguin Pi robot}\label{fig:robot}
\end{figure}

\newpage
\tableofcontents
\newpage

%%%%%%%%%%%%%%%%%%%%%%%%%%%%% INTRODUCTION
\section{Educational objectives}

The mobile robotics learning outcomes we wish to achieve include:
\begin{enumerate}
\item Motion models: how configuration (pose) of the robot evolves with time for key types of platform such as Ackerman steering and differential steering.
\item Motion control: how to design a controller that will move the robot from an initial to a desired final configuration, or to follow a path.  
Initially we will assume that robot configuration is measured (externally) and provided as input to the robot controller.
\item Motion planning: how to find a path to move from A to B
\begin{enumerate}
  \item For a grid-based map that denotes occupied and free space, how to plan an obstacle-free path using the distance transform (aka wavefront or grass fire) algorithm
  \item For a graph-based map using breadth-first, uniform-cost, A* search, or D* algorithms to find an optimal path.
\end{enumerate}
\item Robot localization: how to use observations of known landmarks to estimate robot configuration (``where am I?'').
\item Map making: how to convert landmark observations into a consistent estimated map  assuming that robot configuration is known.
\item Simultaneous localization and mapping: how to create a map and estimate robot configuration based on observations of initially unknown landmarks.
\end{enumerate}

\section{Robot specification}
To explore these learning principles, we require a robot with the ability to move, to report its motion (odometry), to observe landmarks, and make use of an external sensor that reports the robot's configuration.

The robot requires the following features to support these learning outcomes:
\begin{enumerate}
\item Differential-drive platform which is very general.  While quite simple and low-cost to fabricate, 
a software emulation can convert this platform to a virtual Ackerman-steered configuration (the reverse is not true).  
\item A means to provide odometry which is required to estimate current configuration.  Options include:
\begin{enumerate}
  \item Wheel encoders to provide incremental wheel rotation. Ideally these would be quadrature but if motion is in only one direction it could be a simpler and cheaper non-quadrature encoder.
  \item An optical mouse chip to measure x- and y-axis displacement of a point on the robot relative to the ground.  %The ADNS2620 was ideal but now obsolete and there is no obvious replacement.
\end{enumerate}

\item Camera to observe landmarks for localization or visual odometry.  There are many options and the choice could be part of the
student's exercise. Options include:
\begin{enumerate}
  \item Front-mounted forward-looking perspective camera with a limited field of view.
  \item A $360^\circ$ panoramic camera, and there are some low-cost options such as the \href{https://www.robotshop.com/en/arducam-arduino-panorama-360-shield.html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}{ArduCAM (based on 4 regular cameras}.
  \item  An upward-facing \href{https://www.raspberrypi.org/magpi/building-a-raspberry-pi-360-camera/}{catadioptric camera using a low-cost iPhone camera adaptor}.
\end{enumerate}

\item Battery and a means to charge it, ideally while the battery is connected to the robot and the robot is powered up.  Also the
ability to monitor battery voltage.
  \item WiFi communications for tether-less operation. Ideally able to work in the university lab, a student's home or even act as a wireless access point to allow operations in areas with no WiFi infrastructure.

\item An external localization service to provide an estimate of the robot's pose as an input to a motion controller.  This capability will be used initially until students have mastered the techniques to perform localization themselves.  After that, the external localization can be used to provide a ground truth for comparison purposes.  Some options for an external localizer include:
\begin{enumerate}
\item Dead reckoning based on wheel encoders, implemented onboard the robot at a relatively high sample rate.
\item An overhead camera, looking down at distinctive visual markers/beacons on the robot, possibly infra-red (IR) LEDs.
\item A camera on the robot looking up at specialized markers on the ceiling, for example the \href{https://github.com/gestom/whycon-orig.git}{WhyCon system}.
\item Two IR receivers working with one (maybe two) \href{https://en.wikipedia.org/wiki/HTC_Vive}{HTC/Valve Vive base stations} which scan planes of IR light across the workspace.
\end{enumerate}

\item Convenient programming environment for code running either onboard or offboard the robot.  In either case it would be useful to have graphical display of the robot's state and its perceived environment.  For code running offboard the robot, communications latency is likely to be an issue.
Possible programming paradigms include:
\begin{enumerate}
\item Student MATLAB running offboard and communicating via a simple API with provided software running on the  robot 
\item Student Python code running onboard using a Python API
\item Student MATLAB code running in MATLAB Online (in the cloud so no need for a local MATLAB instance) communicating via a simple API with either the low-level robot hardware or provided software running on the robot 
\item Student MATLAB code, using a simple API, compiled to C code and running onboard the robot.
\end{enumerate}

\end{enumerate}

%%%%%%%%%%%%%%%%%%%%%%%%%%%%% ROBOT COMPUTE
\section{The PenguinPi robot}
The robot is shown in Figure \ref{fig:robot-annotated}.
It was developed as a final year student project by Jack Wright in 2016.
Jack was also a student of the EGB439 Advanced Robotics
unit, which at that time used Lego Mindstorm for the practical work.
The robot was refined by Jack and Steven Bulmer over the summer of 2016/7 and the Mark I was used for
the class in 2017 and for a workshop at the Robotic Vision Summer School in early 2018.
A Mark II version was developed over the summer of 2017/8 and used for  class in first semester of 2018.
In the second half of 2018 the onboard software was substantially refactored and extended.

\subsection{Computing systems}
The main processor is a Raspberry Pi 3B with an attached camera (PiCam). 
It includes a microSD card slot, four USB ports, built in BlueTooth and WiFi and an HDMI port and a 40-pin expansion connector.
The operating system is Rasberian and includes python and OpenCV.  ROS is not pre-installed.
By connecting an HDMI monitor plus USB keyboard and mouse the Raspberry Pi provides a capable standalone Linux system with windowed desktop environment.
For mobile operation we use WiFi and connect to it using \texttt{ssh} or web services.
We prefer a 5\unit{GHz} USB dongle over the onboard 2.4\unit{GHz} WiFi capability to avoid congestion in lab sessions with many 
robots.

\begin{figure}
\centering
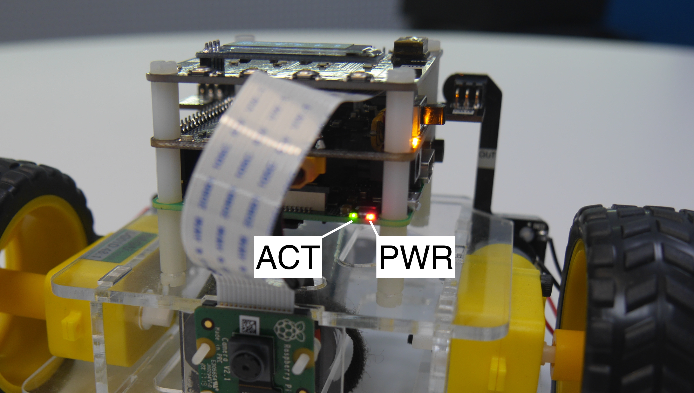
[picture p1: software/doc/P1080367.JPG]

\caption{Raspberry Pi LED indicators}\label{fig:pi-leds}
\end{figure}

The Raspberry Pi 3B has two LEDs to the right of the microSD card slot shown in Fig \ref{fig:pi-leds}:
\begin{itemize}
\item ACT (green) indicates that the SD card is being read or written.  A repetitive pattern of flashes at startup indicates issues
with the SD card or boot process;
\item PWR (red) indicates that the board is powered (it will flash for voltage below 4.63\unit{V}).
\end{itemize}

Alternative computer platforms would include:
\begin{itemize}
\item  BeagleBone Blue, but by comparison  the Raspberry Pi 3 has several key advantages:
 half the cost, has a low-cost camera and interface, and is easy to expand for i/o without needing specialised cables.
\item  Libre computer Le Potato or Renegade
\end{itemize}

The PenguinPi daughter board (PPI) is a Raspberry Pi expansion board that attaches to the Pi's 40-pin expansion connector.
It contains an Atmel 644 8-bit processor with 64k program space and 4k of RAM.  It performs motor control, power management and supports a simple user interface (UI), has a number of indicator LEDs.
It can be expanded by an additional ``hat'' board.
One such board -- HAT1 -- provides infra-red beacon LEDs and a simple user interface comprising push buttons and a small OLED display.

The RaspberryPi and the PPI processors communicate over a high-speed serial port for message exchange, error diagnostics (from the PPI) and display of text strings on the OLED display.

\begin{figure}
\centering

\caption{Annotated view of the Penguin Pi robot}\label{fig:robot-annotated}
\end{figure}

%%%%%%%%%%%%%%%%%%%%%%%%%%%%% ROBOT HARDWARE
\subsection{Robot hardware}
\subsubsection{Motors}
The robot is driven by a pair of ROB-13302 brushed permanent-magnet DC gearmotors with a right-angle gearbox and a reduction ratio of 48:1.  Specifications are:
\begin{itemize}
\item voltage 4.5\unit{V}
\item no load maximum speed of 140\,RPM
\item no load current 190\unit{mA}, this is effectively the Coulomb friction torque
\item maximum load current 250\unit{mA}
\item maximum torque 800\unit{gf \cdot cm} or $0.8 \times 9.81 \times 0.01 =  78.4\unit{mN}$. 
If this is the nett torque \textit{after} friction, then  the torque constant (including gearbox) is $78.4/(250-190) =1.31\unit{N \cdot m/A}$.
The back EMF constant would therefore be 1.31\unit{V\cdot s/rad}.
\end{itemize}

The wheels are ROB-13259 with a diameter of $D=65\unit{mm}$.

\begin{figure}
\centering

\caption{Closeup view the Penguin Pi robot showing the motor, the encoder disk and the PCB which holds the Hall-effect sensors, and 
which plugs into the PPI board.}\label{fig:robot-closeup}
\end{figure}

The motor shaft, before the gearbox, is fitted with an ROB-12629 encoder disk which has 8  poles (4 north poles and 4 south poles) which can be
seen in Figure \ref{fig:robot-closeup}.

\subsubsection{Motor speed response}\label{sec:motor-control}

The response of the motor to applied voltage (percentage of maximum PWM) is shown in Figure \ref{fig:motor-response}. 
It fits well to a line through the origin with a slope of 11.5 but at command below 30 the effect of friction becomes
evident, with no motion for a command of 9 or less.
The maximum encoder rate is 1100\unit{enc/s} or 2.87\unit{rev/s} which is approximately 25\% higher than the motor's rated speed
of 140\,RPM or 2.33\unit{rev/s} -- perhaps indicating that the maximum applied voltage is higher than the motor's specified maximum.

\begin{figure}
\centering

\caption{Open-loop motor response to applied PWM voltage (percentage) for motor A.}
\label{fig:motor-response}
\end{figure}

Ignoring motor inductance  we can write motor current as
\begin{equation}
i = \frac{V - V_b}{R} \label{eq:current}
\end{equation}
where $R$ is motor armature resistance and
\begin{equation}
V_b = K_b \varpi \label{eq:bemf}
\end{equation}
is the back EMF where $K_b$ is the back EMF constant.
Nett motor torque is
\begin{equation}
\tau = \left\{ \begin{array}{ll} 0 & |K_\tau i| \le \tau_C \\ K_\tau i - B\varpi - \mathrm{sgn}(\varpi )\tau_C & |K_\tau i| > \tau_C \end{array} \right. \label{eq:torque}
\end{equation}
where $B$ is viscous friction, $\tau_C$ is Coulomb friction (assumed symmetric) and $K_\tau$ is the motor torque constant.

While moving at steady state, nett torque $\tau = 0$, we can substitute \eq{eq:current} and \eq{eq:bemf} into \eq{eq:torque} to obtain
\begin{equation*}
K_\tau \frac{V - K_b \varpi}{R} - B\varpi - \tau_C = 0
\end{equation*}
and simplifying with $K = K_b = K_\tau$ then
\begin{equation}
\varpi = \frac{K V - \tau_C R}{K^2 + BR} = V \frac{K}{K^2 + BR} -   \frac{\tau_C R}{K^2 + BR}
\end{equation}
which is similar in appearance to Figure \ref{fig:motor-response}.  From the slope (11.95) and breakpoint (-33.74) , and assuming knowledge of $K$ and $\tau_C$ from above, we could estimate $R$ and $B$.

The resulting motor speed ignores disturbance torque from wheel-ground interaction which will be highly dependent on the ground material and  be significant during skid steering.  To overcome this a motor velocity controller can be enabled by setting switch 4 of the DIP switch to ON.
It may be possible to estimate  friction characteristics from the measured battery current.

%%%%%%%%%%%%%%%%%%%%%%%%%%%%%%%%%%%%%%%%%%%%%%%%%%%%%%
%%%%%%%%%%%%%%%%%%%%%%%%%%%%%%%%%%%%%%%%%%%%%%%%%%%%%%
\subsection{Penguin Pi expansion board (PPI)}
The Penguin Pi (PPI) is a small circuit board that connects to the Raspberry Pi GPIO connector.  
It manages a LiPo battery, drives the motors, and interfaces with motors, encoders and a number of LEDs.

\subsubsection{Encoders}

The sensor is an \href{https://www.google.com/url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}{Allegro A1120 unipolar Hall-effect sensor} which turns on when it sense a magnetic south pole.
The motor shaft is fitted with an ROB-12629 encoder disk which has 8  poles (4 north poles and 4 south poles), so the sensor output will have four on-periods and four off-periods per shaft revolution.
The processor is configured to interrupt on changes to the encoder signal (rising and falling edges) of which there are
eight per revolution.  Given the 48:1 gearbox ratio there will be $48 \times 8 = 384$ encoder interrupts per wheel revolution.

The encoder, and the encoder sensing board can be
seen in Figure \ref{fig:robot-closeup}.  This board, which connects to the main PPI board eliminates a lot of point-to-point wiring which 
 led to high build time and poor reliability with the Mark 1 robot.

%%%%%%%%%%%%%%%%%%%%%%%%%%%%% SPEED CONTROL
\subsubsection{Motor driver}\label{sec:motor-control}
The motor voltages are controlled via 8-bit PWM motor drivers with values in the range 0 to 255.
This is performed by Timer 0 and the output compare registers OCR0A and OCR0B.
Motor direction, or applied polarity, is controlled by digital outputs PB0 and PB1 respectively.

 The software considers motor commands in the range -100 to +100 are these are mapped to PWM settings in the range 0-255 plus motor direction.

\subsubsection{Atmel clocks and timing}
The processor has a 20\unit{MHz} external crystal connected between pins XTAL1 and XTAL2.  
The clk$_{\mbox{I/O}}$ signal (20\unit{MHz}) from the clock control logic is used for all timers.  
The clk$_{\mbox{I/O}}$ signal is controlled
by the:
\begin{itemize}
\item Clock source multiplexer, which is set to external crystal oscillator (CKSEL bits in the \texttt{lfuse} fuse byte)
\item System clock prescaler is bypassed, ie. no prescaler (CKKPS bits in the \texttt{lfuse} fuse byte)
\end{itemize}

This clock drives the following counters:

\begin{table}[h]
\begin{tabular}{|l|l|l|} \hline
Timer & Width (bits) & Purpose \\ \hline
0 & 8 & motor PWM \\
1 & 16 & 1\unit{ms} clock interrupt \\
2 & 8 & additional PWM \\ \hline
\end{tabular} 
\end{table}

All counters have the timer prescaler bypassed and clock at 20\unit{MHz}.

\begin{table}
\begin{tabular}{|l|l|l|l|l|l|l|} \hline
Pin &  binary in & binary out & analog & PWM & other & RPi  \\ \hline\hline
PA0 & ENCA1* &&&&&\\
PA1 & ENCA2* &&&&& \\
PA2 & ENCB1* &&&&& \\
PA3 & ENCB2* &&&&& \\
PA4  & HAT06 &&ADC4&&& \\
PA5  &HAT01  &&ADC5&&&\\
PA6 &-&& VSENSE &&& \\
PA7&-&& CSENSE &&& \\ \hline\hline
PB0 &-& DIRA &&&& \\
PB1 &-& DIRB &&&& \\
PB2  & HAT02  &&&&&\\
PB3/OC0A &&&& PWMA && \\
PB4/OC0B &&&& PWMB && \\
PB5 && shutdown request &&& MOSI\textdagger & GPIO10 \\
PB6 &-&&&& MISO\textdagger & GPIO9\\
PB7 &-& shutdown ack&&& SCLK\textdagger& GPIO11 \\ \hline\hline
PC0 &-&&&&SCL\textsuperscript{I2C}& GPIO3\textsuperscript{I2C}\\
PC1 &-&&&& SDA\textsuperscript{I2C} & GPIO2\textsuperscript{I2C}  \\
PC2 && LEDY0 &&&& \\
PC3 && LEDY1 &&&& \\
PC4  & pullup &&&&& \\
PC5 && LEDY2 &&&& \\
PC6 & HAT00 &&&&&\\
PC7  & HAT07* &&&&&\\ \hline\hline
PD0 &-&&&& UART0 RX& UART TX\\
PD1  &-&&&& UART0 TX& UART RX \\
PD2 & HAT05 &&&&&\\
PD3 & HAT03 &&&&&\\
PD4 & HAT04 &&&&&\\
PD5/ICP3 &&&& LEDG &&\\
PD6/OC3A &&&& LEDB &&\\
PD7/OC3B &&&& LEDR &&\\ \hline
\end{tabular}
\caption{Allocation of Atmega i/o ports. * indicates pin-change interrupt is enabled.  Ports A-D generate interrupts on PCINT0 to PCINT3 respectively.
\textdagger indicates used for reprogramming the Atmega.
{}\textsuperscript{I2C} indicates used for I2C bus}\label{tab:io}
\end{table}

\subsubsection{Power}
The PPI connects to a LiPo battery and has a power input socket and a slider ``POWER'' switch.
When the switch is:
\begin{description}
\item[OFF]  the battery is connected to the charging socket, the battery charges but no power flows to the PPI.
\item[ON]   the battery is connected to the PPI, the PPI is powered but the battery cannot charge.  Power flows to the Raspberry Pi via the expansion connector, pins 2 and 4.
\end{description}

If the Raspberry Pi is powered via its micro-USB connector then the PPI will  be energized by power flowing in from the expansion connector (reverse current flow to normal operation).
This is not a recommended way of operation but if attempted, the PPI power switch \emph{must be OFF} and the current available is limited so the motors can provide only limited torque.

\subsubsection{Analog channels}
Voltages are measured by a 10-bit analog to digital converter (ADC) with an 8-channel multiplexer and a reference voltage of $V_{\mbox{cc}} =3.3\unit{V}$.  The PPI uses the ADC to measure:
\begin{itemize}
\item Battery voltage (ADC 6). A voltage divider across the battery rail has a scale factor of 0.20\unit{V/V} giving an ADC scale factor of
$3.3/1024/0.2 = 16.11\unit{mV/count}$.
\item Battery current (ADC 7). A 0.05\unit{\Omega} shunt resistor and a TSC888B current sense amplifier (gain of 20) gives an ADC scale factor of $3.3/1024/0.05/20 = 3.223\unit{mA/count}$.
\end{itemize}

The ADC clock uses a pre-scaler divisor of 64 giving a clock of 312\unit{kHz}.  The first conversion takes 25 cycles (80\unit{\mu s}) and subsequent conversions take 13 cycles (42\unit{\mu s}).

\subsubsection{I2C interface}

The I2C (or TWI) interface is a high-speed two-wire interface for the Atmega processor.
The I2C bus is clocked at 400\unit{kHz}.  Each frame has a start condition, 9-bit address, and then N data bytes, each taking 9 bit times (including the acknowledge bit).
Communications is performed using polled i/o so an N-byte packet requires 9N+20 bit times to transmit or receive, and one bit time
is 2.5\unit{\mu s}.

\subsubsection{LEDs}\label{sec:leds}
There are four physical LEDs on the PPI base board: one RGB LED (LED1), and three yellow LEDs (LEDS 2 to 4).
They are located to the left of the battery connector and numbered increasing from left to right.
All LEDs are connected between Vcc and the Atmel i/o pin and are lit when the pin is at a low voltage and sourcing current.
The RGB LED is considered by the software as 3 separate LEDs (red, green and blue).  

\subsubsection{Atmel I/O ports and interrupts}
The Atmel has four 8-bit digital i/o ports: PA, PB, PC and PD.  Bits can be configured individually as inputs, outputs or open circuit.  Most Atmel pins are 
multi-purpose and the digital i/o capability might be unavailable if an alternative function is used on that pin.
The usage of the i/o signals is described in Table \ref{tab:io}.

Each of the 32 digital i/o pins can generate a pin-change interrupt (PCINT0 to PCINT31) configured on either a rising or falling edge.
There are only 4 interrupt vectors (PCINT0-7, 8-15,16-23, 24-31) and the associated interrupt handler must determine which of the 8 pins changed.

\begin{table}
\centering
\begin{tabular}{|l|l|l|c|} \hline
Pin & Purpose  & GPIO & 40-pin connector\\ \hline\hline
1 & Ground && \\
2 & 5\unit{V} &&  \\
3 & HAT0 & GPIO26 & 37\\
4 & 3.3\unit{V} && \\
5 & HAT1 & GPIO20 & 38\\
6 & HAT7 & GPIO19 & 35\\
7 & HAT2 & GPIO16 & 36\\
8 & HAT6 & GPIO13 & 33 \\
9 & HAT3 & GPIO7 & 26\\
10 & HAT5 & GPIO5 &29\\
11 & SCLK\textdagger (SPI clock) & GPIO2\textdagger & 3\\
12 & HAT4 & GPIO8 & 24\\
13 & PB5/MOSI (SPI data in) & GPIO10\textdagger & 19\\
14 & PB6/MISO (SPI data out) & GPIO9\textdagger & 21\\
15 & PB7/SCL\textsuperscript{I2C} (I2C clock) & GPIO3 & 5\\
16 & SDA\textsuperscript{I2C}(I2C data) & GPIO3\textsuperscript{I2C} & 5\\ \hline
\end{tabular}
\caption{Signals on the PPI expansion connector. 
\textdagger  indicates used for Atmega reprogramming,
{}\textsuperscript{I2C} indicates used for I2C bus,
GPIO refers to the pin on the
BroadCom processor chip, also known as BCM.  The fourth column is the pin number on the Raspberry Pi standard 40-pin expansion connector.  Raspberry Pi GPIO pins can be numbered using either convention.}\label{tab:hat}
\end{table}

\subsubsection{Expansion connector}
The PenguinPi can be expanded with a hat board via a 16-pin connector, Table \ref{tab:hat}, on top of the PPI board.
Some signals connect to the Atmel processor on the PPI board while others connect to the Raspberry Pi via the 40-pin
expansion connector.
Different hat boards could be used to 
support different teaching projects.  

HAT1 supports:
\begin{itemize}
\item An OLED screen is an array of $128\times 32$ pixels.  With a $6\times8$ font this becomes a $21\times4$ array of characters.

\item An array of 4 pushbuttons under the OLED that provide a simple user interface.

\item Four IR LEDs at its corners which are always on.  This requires viewing with an IR sensitive camera, possibly with a
a visible light blocking filter (optical low-pass filter).

\item A DIP switch provides 4 bits of configuration information.  SW4 is used to enable PID motor control, the other bits are available
to the user.

\item A grid of 16 LEDs on the top board can be addressed as a single 16-bit word. The bits are numbered bottom to top, then left to right. The bottom right LED is bit 0 and top left LED is bit 15.
\end{itemize}

Communications with the hat is via I2C messaging and a digital i/o line.  
There are two PCA6416A, 16-bit general purpose I/O expanders, that provides remote I/O expansion via the I2C-bus interface.
One provides 16 outputs for the blue LED array, the other has inputs from the pushbuttons and DIP switch.
The HAT07 line is used to interrupt the PPI when data is available from either PCA6416A, and the PPI will then use the I2C bus to read that data.

\begin{table}
\centering
\begin{tabular}{|l|l|l|l|} \hline
Device & Address & \multicolumn{2}{c|}{Data} \\ \hline\hline
PCA6416A/0 & 0x40 & LEDS 8-15 & LEDS 0-7 \\
PCA6416A/1 & 0x42 & buttons & DIP switch \\
OLED/SSD1306 & 0x78 & command/data & \\\hline
\end{tabular}
\caption{I2C peripherals on PPI HAT1}
\end{table}

\subsubsection{Raspberry Pi expansion connector}
The PPI board is a Raspberry Pi expansion board and the boards are physically and electrically connected by the 40-pin connector
A subset of signals on connector are routed to pins on the Atmel and also the PPI  expansion coonnector.
In summary:
\begin{itemize}
\item it transfers DC power between the PPI and the Raspberry Pi.
\item some Raspberry Pi digital i/o signals (GPIO) are connected to digital i/o signals on the Atmel, see column 7 of Table \ref{tab:io}.
\item some Raspberry Pi  i/o signals (serial, SPI) are connected to pins of the Atmel, see column 7 of Table \ref{tab:io}.
\item some Raspberry Pi i/o signals are passed through to the PPI expansion connector (GPIO, SPI), see Table \ref{tab:hat}.
\item the Atmel can be reflashed by the Raspberry Pi using using the SPI bus while asserting reset.
\end{itemize}

Expansion connector pins are referred to either by pin number or by GPIO number.
The latter refers to the pin on the
BroadCom processor chip, also known as BCM.  Raspberry Pi GPIO pins can be numbered using either convention.
Check online for the pin assignments for a particular type of Raspberry Pi at \url{https://pinout.xyz/pinout}.

\subsubsection{Buttons}
The Atmel can be reset by pushing the RST button or by the Raspberry Pi expansion connector pin 18 (GPIO24).  The Raspberry Pi asserts reset while the Atmel
is being reflashed via the SPI bus.

The SDN button drops Raspberry Pi expansion connector pin 16 (GPIO22), see Table \ref{tab:hat}, to signal that a shutdown is requested.

In \texttt{/boot/config.txt} it is possible to add device tree overlays
\begin{Code}
dtoverlay=gpio-shutdown,gpio_pin=5
dtoverlay=gpio-poweroff,gpiopin=21,active_low="y"
\end{Code}
The first enables shutdown when GPIO 5 is set low -- no other software is needed.  This works as advertised but does not
provide any feedback to the PPI that a shutdown is underway.
The second line is supposed to assert GPIO 21 when the Raspberry Pi is booting but this in practice this does not happen.

Currently these options are not active.

%%%%%%%%%%%%%%%%%%%%%%%%%%%%%%%%%%%%%%%%%%%%%%%%%%%%%%%%
%%%%%%%%%%%%%%%%%%%%%%%%%%%%%%%%%%%%%%%%%%%%%%%%%%%%%%%%

\section{PPI robot software}

%%%%%%%%%%%%%%%%%%%%%%%%%%%%% CODE STRUCTURE

\subsection{Code structure}
The code is organized as one large polling loop with several interrupt handlers.

\subsubsection{Interrupt handlers}
The interrupt sources, and their actions, are:
\begin{itemize}
\item Timer 1 (16-bit clocked at 20\unit{MHz}) interrupt every 1\ms:
\begin{itemize}
\item Every 20 ticks performs the velocity control (50\Hz)
\item Every 10 ticks (offset from above) triggers ADC conversion (100\Hz)
\item Every 50 ticks (offset from above) request the main loop to update the OLED display (20\Hz)
\item Decrement the LED counters
\item Updates the 32-bit system timer counters: \texttt{milliseconds\_counter}, \texttt{seconds\_counter}
\end{itemize}
\item Encoder signal change (rising and falling edge) updates the motor-state structures \texttt{motorPosition}
\item ADC conversion complete, changes the multiplexer settings and stashes data for action by the main loop
\item HAT7 indicates data available from the hat board (push buttons or change to DIP switch), raise a flag for action in the main loop to read the new I2C data
\item Serial port transmit and receive (defined in \texttt{lib/uart.c}) which implements a 64-byte receive data ring buffer.
\end{itemize}

The interval for velocity control, ADC conversion and OLED update are controlled by constants at the top of \texttt{main.c}.

\subsubsection{Main polling loop}
The tasks in the main loop include:
\begin{itemize}
\item Check for a received start byte, and if found read and parse the rest of the message.
The datagram read is effectively blocking for up to the receiving time for 10 bytes, which is 0.87\ms, plus whatever time is
required for processing the message.  
\item When requested by the timer interrupt handler, update the OLED display.  This is a time consuming operation, the I2C communications will take at least 15\ms\ and is performed in 33 chunks spread across successive loops to minimize latency.
\item Update the LED state machines, see Section \ref{sec:leds}.
\item Digitally filter  battery current and voltage if flags set by ADC interrupt handler indicate that new ADC data is available.
\item Test for low battery voltage and take appropriate action.
\item If signalled by the HAT7 interrupt handler, read data from the hat via the I2C port including the DIP switch and the button status.
\item Measure loop time and update statistics
\end{itemize}

Time statistics are updated and available via the OLED ``loop time'' screen. The mean time is only 64\us\ with a maximum of
just under 2\ms. 

\subsubsection{Encoders}\label{sec:encoder}
The PPI hardware supports one or two Hall-effect sensors for each motor encoder.  They are connected to the PA digital input pins
and generate ``pin change'' interrupts.

The encoder count is maintained as a signed 16-bit value.  The counters increase when the robot moves forward.
The counters will wrap  (ignoring overflow) around above 32767 or below -32768.  This is 85 wheel revolutions or 17\unit{m} of travel forwards or backwards.

The advantage of considering the encoders as signed values is that taking the difference on either side of the wrap will result in the correct value, ie. using signed 16-bit arithmetic -32768-(32767) = 1 (positive rotation) and 32767-(-32768) = -1 (negative rotation).

The encoder interrupt handler supports several encoder modes:
\begin{enumerate}[start=0]
\item Single sensor.
The Hall-effector sensor outputs one pulse per south-magnetic pole.  Direction of rotation cannot be determined but can be inferred from the polarity of the applied motor voltage and the counter is incremented or decremented accordingly.
If the motor PWM is zero (idle) the direction is indeterminate and the counters are not updated.
Note that for very rapid changes in motor voltage polarity, the mechanical inertia of the system means that the motor
direction may be opposite to the motor polarity for a short period which will cause odometry errors.

\item Dual quadrature sensors.
At every edge (rising or falling) on the encoder A signal we determine direction of rotation from the value of the quadrature encoder B signal, and increment or decrement the counter accordingly.

\item XOR mode.
At every edge (rising or falling) on the encoder A or B signal we determine direction of rotation from the value of the other signal, and
increment or decrement the counter accordingly.  This leads to a doubling of angular resolution and improved velocity estimation.
\end{enumerate}

\subsection{Motor velocity control}
%The PPI implements two motors control algorithms (when bit 4 of the DIP switch is ON):
%\begin{enumerate}
%\item Wheel angle controller, currently commented out, is a PID controller on encoder value. PID parameters can be set via the communications interface, but the values on the Atmel side are $128t\times$ the apparent value on the Python side.
%Velocity P gain cannot be set.
%\item \end{enumerate}

The velocity control is invoked every 20\unit{ms} when DIP switch 4 is ON.
It runs in the context of the timer interrupt handler, but with interrupts enabled.
While it might be questionable practice to run a control algorithm within an interrupt handler it totally eliminates jitter compared to the 
alternative of settting a flag and having the main loop deal with it.

From Figure \ref{fig:motor-response} we see the maximum encoder rate is 1100\unit{enc/s} which is  22 encoder counts within the 20\unit{ms} sample interval.
The speed command $V^*$ is in the range -100 to +100 so to interpret this as a speed command we first scale it by $1/5$
 to obtain the desired number of encoder counts per control interval (alternately we could scale up the estimated velocity by 5).
The downside of this simple strategy is a very quantized speed signal, with only 20 effective speed settings.
This could be ameliorated by: using a longer servo interval, using an omnidirectional Hall-effect sensor ($\times 2$ improvement) or quadrature
encoders ($\times 2$ improvement) or encoder mode 2 (see Section \ref{sec:encoder}).

Velocity estimation is performed by differencing the current and previous encoder values (signed 16-bit).
The controller is a PI controller with gains $K_{vp}$ and $K_{vi}$ and these parameters
 can be read or written using the commands MOTOR\_SET\_KVP and MOTOR\_SET\_KVI.
The desired velocity is set with the command MOTOR\_SET\_VELOCITY and is in the interval [-100, 100].

All arithmetic is performed using 16-bit signed integers.
The state and control parameters for each motor are kept in a \texttt{Motor} structure, one per motor.

The steady-state closed-loop speed is
\[
\frac{V^*/5}{T}\unit{enc/s}
\]
where $V^*$ is the demanded speed (-100 to +100) and $T$ is the sample interval.
The closed loop gain is therefore $V^*/5/\sci{20}{-3} =  10 V^*\unit{enc/s}$.

In terms of rotational velocity the scaling is 
\[
10 V^* \frac{1}{384} = 0.026V^* \unit{rev/s}
\]
and the translational velocity scaling is
\[
0.026 V^*  \pi D = 5.33V^* \unit{mm/s}
\]

\subsection{Analog channels}

The first ADC reading (voltage) is triggered at 100\Hz\ by the clock interrupt handler and the ADC interrupt handler retrieves the result and initiates the second conversion (current).

Once the second conversion is complete the samples are smoothed by a simple first-order unity-gain digital filter executed in the main loop 
\[
y_{k+1} = b  y_k + (1-b)u_k
\]
which has a pole at $z=b$ which is related to the continuous time pole with frequency $f$ by $z = e^{-2\pi f/T}$.  For example, a pole at 5\Hz\ requires a discrete-time pole
at $z=0.9875$.
The scale factor and digital filtering are implemented in floating point within the main polling loop.

The raw value is obtained with the command ADC\_GET\_VALUE, the smoothed value with ADC\_GET\_SMOOTH, and the digital pole is set with
ADC\_SET\_POLE.

\subsection{Battery monitoring and low-voltage actions}
If battery voltage falls below 7\unit{V} the screen colors are inverted: black text on white background.
Once the voltage falls below 6.5\unit{V} for a specified number of cycles then a Raspberry Pi shutdown is initiated via GPIO22.
The main loop is blocked by an infinite loop which disables all buttons and screen updates. 

\subsection{Measuring time}
Functions exist to measure time to an accuracy of 0.05\unit{\mu s}.  
The \texttt{timer\_t} object represents time and contains a snapshot of the seconds, milliseconds and 20\unit{MHz}  counter.
The function \texttt{timer\_diff\_us} computes the difference between two of these objects in units of microseconds.

\begin{Code}
#include "timer.h"

timer_t t0, t1;

timer_get(&t0);
 .
 .
timer_get(&t1);

uint32_t dt = timer_diff_us(&t1, &t0);
\end{Code}

This module also supports simple statistics for \texttt{uint32\_t} quantities
\begin{Code}
stats_t exec_time;

stats_init(&exec_time, dt);
stats_add(&exec_time, dt);
 .
printf("average time %lu\n", stats_mean(&exec_time) );
printf("standard deviation %lu\n", stats_std(&exec_time) );
printf("max time %lu\n", stats_max(&exec_time) );

\end{Code}

\subsection{LEDs}\label{sec:leds}
There are four physical LEDS on the PPI base board: one RGB LED (LED1), and three yellow LEDs (LEDS 2 to 4) which are 
considered  as 6 separate LEDs designated: R, G, B, 2, 3, 4. 
The software interface allows any LED to be:
\begin{itemize}
\item turned on using the command LED\_SET\_STATE,1
\item turned off using LED\_SET\_STATE,0
\item pulsed for a period of time using LED\_SET\_COUNT,T. This is an unsigned 8-bit number of milliseconds, so the maximum on period is $0.255\unit{s}$
\end{itemize}

Each LED has some associated software state that is used by the timer interrupt handler and the main loop.  It contains:
\begin{description}
\item[state] either 0 (off) or 1(on).  Set by a command or the PPI code itself. In every cycle of the main loop the LED is
turned on or off according to this state.
\item[count] if non-zero it is decremented every millisecond and when it reaches zero the state is set to off.
\end{description}

If count is set to a non-zero value the state is set to on, and it will then count down and when it reaches zero the LED will be turned off.

The LEDs can be controlled via the API but they have hardcoded usage in the PPI code (enabled by the \texttt{DEBUG\_LED} macro):
\begin{itemize}
\item Blue, pulse on every start byte, indicating that commands are being received from the Raspberry Pi.
\item Green, pulse on every encoder interrupt.  Note that in encoder mode 0 encoder pulses will not update the encoder counter if the motor is idle (zero applied voltage).
\item Red, long pulse on every serial receive error (framing, overrun or buffer overflow) or bad datagram (overlength, CRC failure).
\end{itemize}

\subsection{Error handling}
Any errors generated by the PPI code are reported by the \texttt{errmessage()} function which has \texttt{printf()} like semantics.
Messages are:
\begin{itemize}
\item sent to  the OLED display ``error'' screen
\item prefixed with \texttt{ERR}  and transmitted on the serial connection to the Raspberry Pi where the Python library will send them 
to the logging channel (stderr).
\end{itemize}

\subsection{Shutting down}
A shutdown can be initiated by:
\begin{enumerate}
\item Pressing the SDN button on the rear end of the PPI board is pushed which directly sets GPIO22 to zero.
\item The Atmel can initiate a shutdown (in the event of low batter) by setting GPIO10 to zero.
\end{enumerate}

A software daemon \texttt{python/GPIOSoftShutdown.py} monitors both GPIO lines and performs simple debouncing.  At startup it
sets GPIO11 to one.
When a shutdown request is detected the daemon:
\begin{enumerate}
\item sets GPIO11 to zero to inform the Atmel that a shutdown is requested.  The Atmel displays the message \texttt{"TURN RaspberryPI OFF SAFELY"}.
\item executes a \texttt{sudo shutdown now} command to shutdown the RaspberryPi.  It will reboot almost straight away so wait until
the disk activity has ceased (ACT LED, see Figure \ref{fig:pi-leds}, has stopped blinking) and then set the power switch to OFF.
\end{enumerate}

The Raspberry Pi cannot actually be shut down, the 
shutdown command is effectively a synonym for reboot so power must be turned off once the ACT LED has stopped blinking.

\subsection{Hat}
The PenguinPi can be expanded with a hat board that fits onto the 16-pin connector on top of the PPI board.
The current hat supports a simple user interface as well as four infra-red LEDs for
localization.  Communications with the hat is via digital inputs and I2C messaging.

\subsubsection{DIP switch}
A DIP switch provides 4 bits of configuration information.  
It can be read using the HAT\_DIP\_GET command. 

\begin{center}
\begin{tabular}{|l|l|l|}\hline
Switch & Bit value & Usage \\ \hline\hline
1 & 8 & \\
2 & 4 & \\
3 & 2 & beacon enable \\
4 & 1 & PI velocity control enable \\\hline
\end{tabular}
\end{center}

The top switch, SW4, is used to enable PID motor control.
Unused switches might be useful to select a particular boot-time network configuration for the Raspberry Pi (eg. home or lab) via a GPIO line sensed
by the Raspberry Pi initialization code.

\subsubsection{More LEDs}

The grid of 16 LEDs on the top board can be addressed as a single 16-bit word. The bits are numbered bottom to top, then left to right. The bottom right LED is bit 0 and top left LED is bit 15.  They can be set by HAT\_LEDARRAY\_SET.

\subsubsection{LED beacons}

The hat board contains 4 IR LEDs at its corners which are always on.  This requires viewing with an IR sensitive camera, possibly with a
visible light blocking filter (optical low-pass filter).

Alternatively we could view a beacon pattern on the $4\times 4$ blue LED matrix.  An L-shaped pattern can be enabled by setting
switch 3 of the DIP switch or by using the command HAT\_LEDARRAY\_BEACON.

\subsubsection{Buttons}
An array of 4 pushbuttons on the OLED hat provide a simple but effective user interface.  From left to right:
\begin{enumerate}[start=0]
\item Select the next information screen on the OLED display.
\item Stop all motors.
\item Screen specific.
\item User button, HAT\_BUTTON\_GET returns the number of times the button has been pushed since the last invocation.
\end{enumerate}

\subsubsection{Screens}
The OLED screen is an array of $128\times 32$ pixels.  With a $6\times8$ font this becomes a $21\times4$ array of characters.
The software supports a number of ``screens'' which are
selected by button 0 (mentioned above).  The screens are:
\begin{enumerate}
\item Network IP address, shown at startup
\item User data, received text that is not part of a datagram is scrolled. Button 2 clears the screen.
\item Battery status: voltage and current
\item Motor command values
\item Encoder values. Button 2 resets the encoders.  Note that in encoder mode 0 if the motor voltage is zero (motor's idle) these values
will not change when the wheels are turned.
\item Motor controller data. Button 2 sets the right motor to speed of -20 and left motor to speed of +20.
\item Loop timing statistics
\item System statistics
\item Error messages. Button 2 clears the error message.
\item Last datagram received.
\end{enumerate}

The error screen becomes the current screen whenever an error message is posted.

The screen background is normally black, but becomes white (inverted text) when the battery voltage falls below 7\unit{V}.

\subsection{Code organization}

\begin{center}
\begin{tabular}{|l|l|} \hline
File & Purpose \\ \hline
\texttt{main.c} & main entry point \\
\texttt{datagram.c} & all RPi communications \\
\texttt{motor.c} & timer measuring and stats \\
\texttt{timer.c} & timer measuring and stats \\
\texttt{io.c} & board hardware support \\
\texttt{hat.c} & hat specific code \\
\texttt{lib/uart.c} & serial interface \\
\texttt{lib/twi.c} & I2C interface \\ \hline
\end{tabular}
\end{center}

\subsection{Programming the PPI}
The CPU is an ATmega644PA.
The C source code for the PPI is provided on the Raspberry Pi along with a cross-compiler toolchain.  To build the code is simply
\begin{Code}
% make
\end{Code}

The RaspberryPi can act like an ISP (\texttt{pi\_isp}) to facilitate flashing the Atmel on the PPI board via certain lines in the GPIO connector.
The code can be flashed on to the PPI 
\begin{Code}
% sudo make load
\end{Code}
which uses \texttt{avrdude}.

It is important to use \texttt{sudo} to achieve permission to access the Raspberry Pi i/o signals which are used for reflashing.
In the event of error messages about the GPIO being busy (this occurs if the reflash is attempted without sudo) the condition can be cleared by
\begin{Code}
% sudo echo 24 > /sys/class/gpio/unexport
\end{Code}
Note that sometimes the Raspberry Pi will reboot after the Atmel is reflashed.

The fuse values can be read by
\begin{Code}
% sudo  avrdude -c pi_isp -p atmega644p
\end{Code}
and should be: E=0xff, L=0xff, H=0xd9. 

For a brand new PPI board these will not be set correctly and the PPI board will appear to run very slowly, the LED sequence at boot time and the UI.  To set the fuses correctly use
\begin{Code}
% make fuse
\end{Code}

More information about fuse settings can be found at the online fuse calculator at \url{http://www.engbedded.com/fusecalc}.

\subsection{The Git repository}
The code currently resides in the Bitbucket repository:

\texttt{https://bitbucket.org/serenamou/egb439/src/master}.

%%%%%%%%%%%%%%%%%%%%%%%%%%%%%  
\section{Communications protocol}\label{sec:comms}
The Raspberry Pi and the PPI communicate using datagram messages over a high-speed serial port.

\subsection{Serial communications channel}
The devices communicate over a bidirectional asynchronous serial port at  at 115,200 baud with one stop bit, no parity and no flow
control -- that is  one byte every 87\unit{\mu s}.

The Raspberry Pi sends and receives data packets on \texttt{/dev/serial0}.
The RaspberryPi 3 SoC has two UARTS: a high-performance UART connected to the BlueTooth device (by default) and a low-performance
``mini UART'' connected to the GPIO serial port pins and designated as \texttt{/dev/serial0}.
The mini UART has an 8 symbol hardware FIFO receive buffer. 
We rely on the Linux kernel device driver to retrieve characters in a timely manner from the UART to prevent 
data overrun.
The high-performance UART (PL011 with 32 byte hardware buffers) requires configuring a hardware overlay.
The PySerial 3.4 package provides a convenient interface to the serial port.

The Atmel processor has two UARTS: UART0 and UART1. Each has a 3 byte hardware buffer: serial shift register and a 2-level FIFO buffer.
Communications is handled by \cite{Fleury}.  It implements interrupt driven circular buffers, with default size 64, to manage serial data in both directions.  
The buffer length is much greater than a
serial packet length so if interrupt latency is kept below 3 character times (270\unit{\mu s}) it is possible to avoid missing any incoming characters.
The function \texttt{uart\_getc} returns a 16-bit value, with the top 8 bits being error flags.  The flags are the UART hardware error flags as well as
a software buffer overrun flag.  These are all defined in \texttt{lib/uart.h}.    
Both UARTs are initialized but only UART0 (Atmel pins 9 and 10) is used. The pins of UART1 (pins 11 and 12) are used for other purposes.

\subsection{Datagram structure}

The datagram message is organized as

\begin{table}[h]
\centering
\begin{tabular}{|c|c|c|c|c|c|}\hline
0 & 1 & 2 & 3 & 4:3+N & 4+N \\ \hline
0x11 & \cellcolor[gray]{0.8} N &  \cellcolor[gray]{0.8}Address &  \cellcolor[gray]{0.8}Command &  \cellcolor[gray]{0.8}Data &  \cellcolor[gray]{0.8}CRC \\ \hline
\end{tabular}
\end{table}

where N is the datagram length, and includes all those elements shown shaded. The minimum length is N=4 for a datagram with no data payload.
The maximum length is 10 bytes but realistically the payload would be at most 4 bytes, that is, N=8. 
The address field indicates which software component the message is destined for, and the command is component specific. 

The command has the top bit set if a response datagram is expected. In this case the return a packet has the same address and opcode and  a finite number of payload bytes.
The type of data, whether signed or unsigned 8-, 16- or 32-bit integer or float depends on the particular command and the sender and receiver code needs to agree on this.
 
The packets are read by the PPI main loop in a blocking read of the entire packet.  The longest packet, including the start byte would take $11 \times 87 = 0.96\unit{ms}$ to receive.
This induces a worst case delay of nearly 1\unit{ms}.
The last datagram received can be viewed on the OLED ``last datagram'' screen.
Non-datagram characters are scrolled on the OLED ``user'' screen which works like a tiny terminal emulator.  Lines are only 21 characters wide and the text is wrapped as required.  Newline ('\textbackslash n') starts a new line and formfeed ('\textbackslash f') clears the screen.

Both the Atmel and \rpi\ ARM processor are little-endian (ie. least significant byte in low address).  The data payload is organized in 
big-endian format which is consistent with standard network byte order.
This introduces extra complexity from gratuitous byte reordering.

A CRC8  is computed with a generator polynomial of 10010111 (0x97).  The algorithm, expressed in MATLAB code, is:
\begin{Code}
        function crc = crc8(msg)
            crc = uint8(0);
            poly = uint8(hex2dec('97'));
            for i=1:length(msg)
                v = vals(i);
                crc = bitxor(crc, v);
                for j=1:8
                    if bitand(crc, 1) > 0
                        crc = bitxor(bitshift(crc, -1), poly);
                    else
                        crc = bitshift(crc, -1);
                    end
                end
            end
        end
\end{Code}

\subsection{Command dispatch}
Once a datagram has been successfully received the appropriate handler function is invoked.  This is executed in the context of the main loop.

The first step is to dispatch the 
datagram to the appropriate  handler function for the particular address (eg. HAT\_OLED) or for a class of addresses (eg. MOTOR\_L and MOTOR\_R share a handler).  This is achieved by a large switch statement.  An unknown address is passed to the hat's device handler \texttt{hat\_datagram} and if it is not recognized there it is flagged as an error.

The device handler function uses another switch statement to dispatch the datagram to the appropriate handler function for the particular command.
 An invalid command is flagged as an error.
 The command handler function:
 \begin{itemize}
 \item checks that the payload length is correct
 \item takes appropriate action based on the payload
 \item if required, creates and queues a return datagram
 \end{itemize}

\section{APIs}
The PPI hardware communicates with the Raspberry Pi over a high-speed serial link using datagram messages.  A number of different
APIs are defined: the serial port, Python interface library, RESTful web services and MATLAB.

\subsection{PPI serial API}

The PPI code maintains an abstraction of devices which are individually addressable:

\begin{centering}
\begin{tabular}{|l|l|}\hline
Address & device \\ \hline\hline
MOTOR\_L & left wheel \\
MOTOR\_R &right wheel \\
LED\_R &  LED1 RGB red channel \\
LED\_G&  LED1 RGB green channel \\
LED\_B&  LED1 RGB blue channel \\
LED\_2 & LED2 yellow \\
LED\_3& LED3 yellow \\
LED\_4& LED3 yellow \\
ADC\_V & battery voltage \\
ADC\_C & battery current \\ 
MULTI & virtual device representing both motors \\ \hline
HAT\_OLED & OLED display on PPI hat board\\
HAT\_LEDARRAY & array of LEDS on PPI hat board \\
HAT\_DIPSW & DIP switch on PPI hat board \\ \hline
\end{tabular}
\end{centering}

Each device responds to a device-specific set of commands.

While this structure is very modular, the most common operation of setting robot speed and reading the encoders requires 4 
transactions: 4 messages transmitted and 2 messages received. For this reason the virtual ``MULTI'' device has been added which
allows a single command to set both wheel velocities and return both encoder counts.

The most primitive method of interfacing with the PPI is by sending and receiving these datagrams over the \texttt{/dev/serial0} using the conventions described in Section \ref{sec:comms}.  There is no C language API for this. 

\subsubsection{MATLAB and Raspberry Pi coder support}
Using the MATLAB coder and Raspberry Pi support package it is possible to write code to communicate with the PPI directly via
the serial port.  Impressively this code could run in the cloud via MATLAB Online.

\begin{Code}
	% PiBot using Raspberry Pi serial port access

        MOTOR_SET_SPEED_DPS = uint8(1);
        MOTOR_GET_DEGREES = uint8(hex2dec('82'));
        STARTBYTE = uint8(hex2dec('11'));
        AD_MOTOR_A 		= uint8(4);
        AD_MOTOR_B 		= uint8(5);
        
        orpi = raspi(ip, 'pi', 'PenguinPi')
        serialdevice = serialdev(rpi, '/dev/serial0', 115200)
            
        send_message(AD_MOTOR_A, MOTOR_SET_SPEED_DPS, int16(speedA));
        send_message(AD_MOTOR_B, MOTOR_SET_SPEED_DPS, int16(speedB));

        function send_message(address, command, value)
            % payload is uint16 big endian, MS byte first
            msg = [address command];
            if nargin > 3
                msg = [msg value2bytes(value)];
            end
            
            msg = [length(msg)+2 msg];
            crc = crc8(msg);
            msg = [STARTBYTE msg crc];
            write(serialdevice, msg);
        end
        
        function readencoder()
            send_message(AD_MOTOR_A, MOTOR_GET_ENCODER);
            m = get_message('int16');
        end
        
        function v = get_message(type)
            % look for the start byte and length
            while true
                c = read(serialdevice, 2);
                if c(1) == STARTBYTE
                    len = c(2);
                    break
                elseif c(2) == STARTBYTE
                    len = read(serialdevice, 1);
                end
            end

            % read the payload
            payload = read(serialdevice, len-1);
            m = [len payload(1:end-1)];
            
            assert(payload(end) == crc8(m), 'Checksum failed')
            
            v = m(4:end);
            if endian == 'L'
                v = fliplr(v);
            end
            v = typecast(v, type);
        end
        
        function msg = value2bytes(obj, val)
            % convert input value of any type into a byte string in 
            % big-endian order
            
            msg = typecast(val, 'uint8');
            
            if obj.endian == 'L'
                msg = fliplr(msg);
            end
        end
 \end{Code}
and have it compiled and executed onboard the Raspberry Pi using MATLAB \texttt{codegen}.

\subsection{Python API}
The Python API \texttt{penguinPi.py} abstracts the PPI devices as Python objects and each object has a set of device-specific methods.  These methods are generally light-weight
wrappers around code that sends a datagram to,   and optionally receives a datagram from, the PPI.
The Python API can be used to support robot applications running onboard the robot. 
The Python API \texttt{penguinPi.py} allows parameters to set or retrieved from the PPI processor.  
The module \texttt{penguinPy.py} build upon the PySerial 3.4 package which provides a convenient interface to the serial port.
The abstract devices implemented in the low-level API and supported by the Python API are listed in Table \ref{tab:devices}.  For example to flash LED3 the following
Python code is required
\begin{Code}
import penguinPi as ppi
ppi.init()
led3 = ppi.Led('AD_LED3')  # create an object representing LED3
led3.set_count(100)      # pulse the LED on for 100ms
\end{Code}

To turn the left motor is
\begin{Code}
import penguinPi as ppi
ppi.init()
left = ppi.Motor('AD_MOTOR_L')
left.set_velocity(30)  # spin the wheel at 30 encs/sample
\end{Code}

A key aspect of this API is that it is thread safe.  A Python mutex locks the serial port resources and enforces serialization of 
requests from threads.  A datagram reading thread is launched at initialisation which processes and checks incoming datagrams and
places them in a queue for return to the thread that requested it.
It is critical that only one thread reads from the PPI.  The datagram reader thread receives datagrams and places them in a queue.  Any other characters are send to the logging channel
with time and data stamping for the first character after a newline.  This allows error messages from the PPI to be monitored on the
Raspberry Pi.
 A POSIX mutex serializes all datagram exchanges with the PPI.  The mutex owning thread can transmit and optionally receive
a response via the datagram queue.

The Python and PPI code need to agree on the numeric values of device address and command codes.  These are defined by enums
in the PPI code \texttt{datagram.h}.  A python program \texttt{defines.py} parses this and saves this as a pickled dictionary \texttt{atmel-symbols.pickle} for use by \texttt{penguinPi.py}. 

\subsubsection{Serial port exclusion on Raspberry Pi}
The PPI code has a single thread reading datagrams and responding to them.  The Raspberry Pi code is more complex, with several processes communicating with the PPI (robot application, IP address daemon).
 A process opens the serial port with  POSIX file locking which is supported by PySerial 3.4.  Once a process has the serial port open, others will fail to connect.

\begin{figure}
\centering
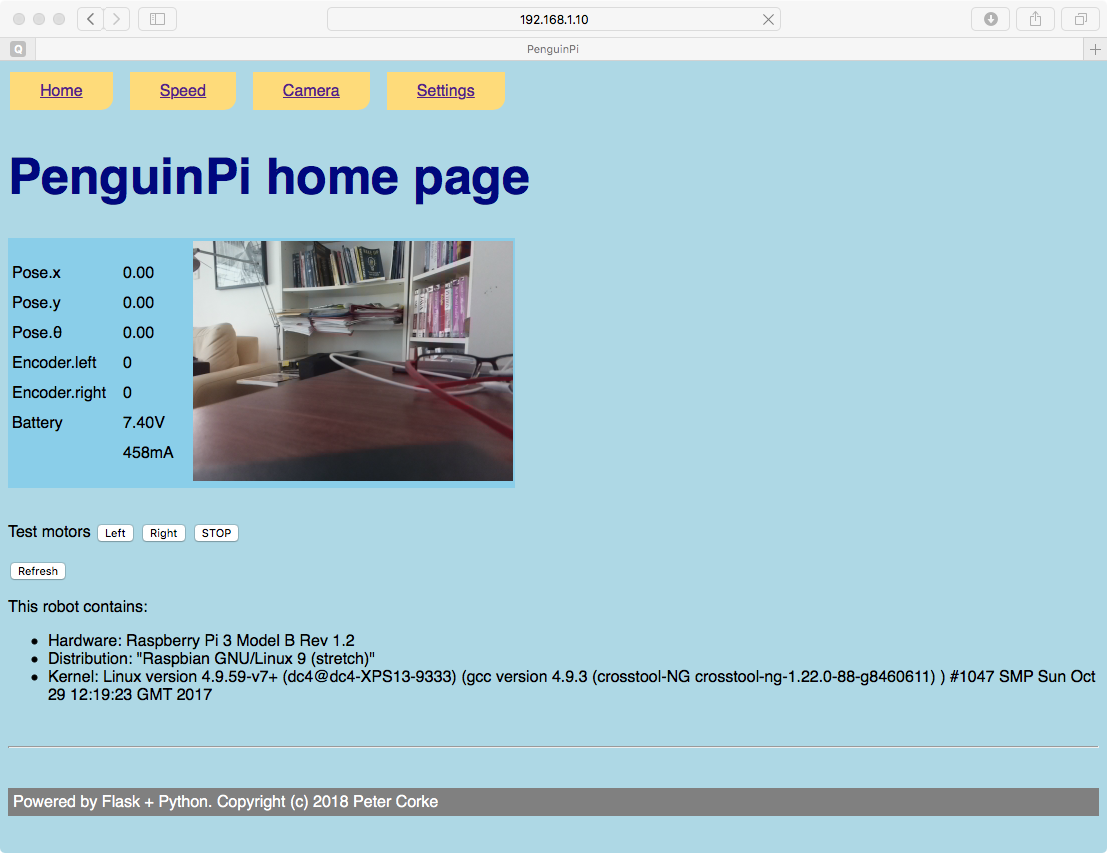
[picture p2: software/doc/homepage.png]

\caption{Home page}\label{fig:homepage}
\end{figure}

\subsection{Boot process}
At boot time a startup script is run via \texttt{crontab} which is edited by \texttt{sudo crontab -e}
\begin{Code}
@reboot bash /home/pi/.startup-servers.sh
#* * * * * bash /home/pi/check_network.sh
\end{Code}
The first line invokes a hidden script in the user \text{pi}'s home directory which invokes the servers to run at boot time.
This used to be separate motor and camera servers, but is now just the \texttt{ppweb.py} server.

The second line, commented out, used to run the IP network update daemon every minute.  That functionality is now 
subsumed by the \texttt{ppweb.py} server.

%%%%%%%%%%%%%%%%%%%%%%%%%%%%% WEB SERVER
\subsection{Web API}
A light-weight web server written using the Flask Python package and is built on the Python API.
It implements  a human-friendly interface to the robot, see Figure \ref{fig:homepage}  as well as a
 RESTful programmatic interface. 
This interface  makes the PenguinPi robot into a network resource which can be controlled
 by any computer on the same network.
 
 In order to use this we must first determine the robot's IP address which is usually assigned by a DHCP server (this depends on its network configuration defined by \texttt{/etc/network/interfaces}).  
 The IP address is displayed on the OLED some time after the Raspberry Pi
has booted.
The web server can be accessed on port 8080 at the robot's IP address.  The home page shows all relevant robot status including 
a snapshot from the robot's camera, encoder values, dead-reckoned pose, battery voltage, motor testing, Raspberry Pi hardware and software details. 
Additional pages, accessible via the navigation bar, allow motor speed setting and camera parameter adjustment.
All pages can be automatically refreshed by adding the query \texttt{?refresh=N} where N is the refresh interval in seconds.

The robot's pose is estimated on board by a thread that performs dead reckoning.  It reads the encoder values at 10\unit{Hz} (default value) and using knowledge of wheel
diameter and wheel separation (distance between the middle of the tyres is used).

Commands are implemented by access to the URLs given in Table \ref{tab:api-xref}.  In addition some higher level functions are provided

\begin{tabular}{|l|l|l|l|} \hline
Operation & URL & Query & Return \\\hline\hline
Set velocity & \texttt{/robot/set} & \texttt{?vel=LEFT,RIGHT} & state \\
 &                      & \texttt{?time=DURATION}  & state\\
 &                      & \texttt{?acc=DURATION} & state \\
Initialize state estimator & \texttt{/robot/pose/reset}   &  &\\
Get image & \texttt{/robot/camera/get} & & image \\
 & &                  \texttt{?resolution=(WIDTH,HEIGHT)} & image \\
 &  &                 \texttt{?awb=AWB} & image\\\hline
\end{tabular}

where state is a JSON message that contains odometry and onboard dead reckoned pose.
The image is returned in PNG format.
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

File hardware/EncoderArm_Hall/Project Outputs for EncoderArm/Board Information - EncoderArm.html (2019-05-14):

Altium customize

# Board Information Report

Date: | | 8/10/2018
Time: | | 12:12:14 PM
Elapsed Time: | | 00:00:00
Filename: | | T:\Techs\Steve\Projects\170327 - PenguinPi_v2\PCB\EncoderArm_Hall\EncoderArm.PcbDoc
Units: | | mmmils

## Contents

Contents

Board Specification

General

Routing

Routing Information

Layer Information

Layer Information

Drill Pairs

Board Holes

Non-Plated Hole Size

Plated Hole Size

Board Slots

Non-Plated Slot Size

Plated Slot Size

Board Square Holes

Non-Plated Square Hole Size

Plated Square Hole Size

Other

Top Layer Annular Ring Size

Mid Layer Annular Ring Size

Bottom Layer Annular Ring Size

Pad Solder Mask

Pad Paste Mask

Pad Pwr/Gnd Expansion

Pad Relief Conductor Width

Pad Relief Air Gap

Pad Relief Entries

Via Solder Mask

Via Pwr/Gnd Expansion

Track Width

Arc Line Width

Arc Radius

Arc Degrees
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

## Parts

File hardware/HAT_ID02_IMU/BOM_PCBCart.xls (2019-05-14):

Manufacturer | Manufacturer Part Number | Designator | Qty | Description | Case | SMD ,BGA,LCC,OR TH | Top/Bottom | points | Total points | Comment
CTS Corporation | 219-4MST | DIP1 | 1 | 4 way slide switch SPST | Gull wing | SMD | Top | 4 | 4
中景园电子 | M091-4PW | OLED1 | 1 |  |  | TH | Top | 4 | 4 | http://www.icstation.com/white-oled-display-module-inch-interface-128x32-oled-screen-module-ssd1306-arduino-p-9933.html
TAD | 1-1602FBV0T | P1 | 1 | HDR2x8 | HDR2x8 | TH | Bottom | 16 | 16 | Part goes on bottom. Soldered on top
Yageo | RC0805FR-0710KL | R1, R2, R3, R4, R5, R6, R7, R8, R9, R10, R11, R12 | 6 | 10k 1% 1/8W 0805 | 0805 | SMD | Bottom | 2 | 12
E-Switch | TL3342F160QG/TR | S1, S2, S3, S4 | 4 | TL 3342 surface mount pushbutton | E-SWITCH-TL3342 | SMD | Top | 4 | 16
NXP Semiconductors | PCA6416APW,118 | U1 | 1 | PCA6416A | 24TSSOP | SMD | Bottom | 24 | 24
Yageo | CC0805KRX7R7BB104 | C1, C2, C6 | 3 | 100nF, 16V, 0805 | 0805 | SMD | Bottom | 2 | 6
TDK Corporation | C2012X5R1C106K085AC | C3 | 1 | 10uF, 16V, 0805 | 0805 | SMD | Top | 2 | 2
Yageo | CC0805KRX7R7BB104 | C4 | 1 | 100nF, 16V, 0805 | 0805 | SMD | Top | 2 | 2
TDK Corporation | C2012X5R1C106K085AC | C5 | 1 | 10uF, 16V, 0805 | 0805 | SMD | Bottom | 2 | 2
Digikey | 1428-1019-1-ND | U2 | 1 | MPU-9250 | QFN | SMD | Top | 24 | 24

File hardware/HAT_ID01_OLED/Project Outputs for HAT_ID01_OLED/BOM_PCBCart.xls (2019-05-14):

Manufacturer | Manufacturer Part Number | Designator | Qty | Description | Case | SMD ,BGA,LCC,OR TH | Top/Bottom | points | Total points | Comment
Digikey | CT2194MST-ND | DIP1 | 1 | 4 way slide switch SPST | Gull wing | SMD | Top | 4 | 4
Digikey | 160-1645-1-ND | LED1 : 16 | 16 | Blue LED | 0805 | SMD | Top | 2 | 32
Digikey | 754-1435-1-ND | LED17 : 21 | 5 | Infrared LED | 0805 | SMD | Top | 2 | 10
 |  | OLED1 | 1 |  |  | TH | Top | 4 | 4 | http://www.icstation.com/white-oled-display-module-inch-interface-128x32-oled-screen-module-ssd1306-arduino-p-9933.html
 |  | P1 | 1 | HDR2x8 | HDR2x8 | TH | Bottom | 16 | 16
 |  | R1, R2, R3, R4, R7, R8, R9, R10, R11, R12, R15, R16 | 12 | 10k 1% 1/8W 0805 | 0805 | SMD | Bottom | 2 | 24
Digikey | YC164J-100CT-ND | R5, R6, R13, R14 | 4 | Surface mount resistor array |  | SMD | Bottom | 8 | 32
 |  | R17, R18, R19, R20, R21 | 5 | 200R 1% 1/8W 0805 | 0805 | SMD | Bottom | 2 | 10
Digikey | EG2531CT-ND | S1, S2, S3, S4 | 4 | TL 3342 surface mount pushbutton | E-SWITCH-TL3342 | SMD | Top | 4 | 16
Digikey | 568-9911-1-ND | U1, U2 | 2 | PCA6416A | 24TSSOP | SMD | Bottom | 24 | 48
 |  | C1, C3 | 2 | 10uF, 16V, 0805 | 0805 | SMD | Top | 2 | 4
 |  | C2, C4 | 2 | 100nF, 16V, 0805 | 0805 | SMD | Top | 2 | 4

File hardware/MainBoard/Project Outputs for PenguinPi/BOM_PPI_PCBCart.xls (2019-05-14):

Manufacturer | Manufacturer Part Number | Designator | Qty | Description | Case | SMD ,BGA,LCC,OR TH | Top/Bottom | points | Total points | Comment
 |  | C1, C2 | 2 | 10uF, 50V 0805 | 0805 | SMD | Top | 2 | 4
 |  | C3 | 1 | 1uF, 50V 0805 | 0805 | SMD | Bottom | 2 | 2
 |  | C4 | 1 | 4u7, 50V, 0805 | 0805 | SMD | Bottom | 2 | 2
 |  | C5, C6, C7, C10, C11, C12 | 6 | 100nF, 50V 0805 | 0805 | SMD | Bottom | 2 | 12
 |  | C8, C9 | 2 | 9pF, 16V, 0805 | 0805 | SMD | Bottom | 2 | 4
Digikey | 1727-5317-1-ND | D1 | 1 | Schottky 30V 5A SOD128 | SOD-128 | SMD | Top | 2 | 2 | Cathode closest to R1
Bourns | MF-MSMF250/16X-2 | F1 | 1 | PTC Resettable Fuse 2.5A | MF-MSMF250/16X-2 | SMD | Top | 2 | 2
Bourns | CM322522-100KL | L1 | 1 | 10uH Inductor | 1210 | SMD | Bottom | 2 | 2
Kingbright | APFA3010LSEEZGKQBKC | LED1 | 1 | RGB LED Right angle | LED RGB RightAngle | SMD | Top | 4 | 4 | LED mounted such that light emitted perpendicular to the board
Kingbright | APA2107LSYCK/J3-PRV | LED2, LED3, LED4, LED7 | 4 | YELLOW LED Right angle | LED YELLOW RightAngle | SMD | Top | 2 | 8 | LED mounted such that light emitted perpendicular to the board
 |  | LED5 | 1 | Red LED, 0805 |  | SMD | Top | 2 | 2 | Cathode closest to U4
 |  | LED6 | 1 | Green LED, 0805 |  | SMD | Top | 2 | 2 | Cathode closest to U4
 |  | LEFT, RIGHT | 2 | 2x3 male pins, right angled | HDR2X3 | TH | Top | 6 | 12 | Mounted on the top, soldered on the bottom with the right angle facing away from the QUT logo. Pic can be provided if needed.
Amass | XT30PW | P1 | 1 | PCB XT30 male connector | XT30 - PCB mount | TH | Bottom | 4 | 4
Digikey | CP1-021PJCT-ND | P2 | 1 | DC Jack |  | SMD | Bottom | 3 | 3
 |  | P4 | 1 | 2x8 male pins | HDR2x8 | TH | Top | 16 | 16
 |  | P5 | 1 | 2x3 male pins | HDR2x3 | TH | Top | 6 | 6
 |  | PI | 1 | 2x20 female socket suitable for a Raspberry Pi | RPI 2 Header | TH | Bottom | 40 | 40 | Component on bottom - Soldered on top i.e. https://core-electronics.com.au/gpio-header-for-raspberry-pi-b-2x20-female-header.html
Ohmite | MCS1632R050FER | R1 | 1 | 0.05R, 1%, 1W 1206 | 1206 | SMD | Top | 2 | 2
 |  | R2, R13 | 2 | 10k, 1%, 1/8W, 0805 | 0805 | SMD | Bottom | 2 | 4
 |  | R3 | 1 | 1.34k, 1%, 1/8W, 0805 | 0805 | SMD | Top | 2 | 2
 |  | R4 | 1 | 27k, 1%, 1/8W, 0805 | 0805 | SMD | Bottom | 2 | 2
 |  | R5, R17 | 2 | 10k, 1%, 1/8W, 0805 | 0805 | SMD | Top | 2 | 4
 |  | R6 | 1 | 6.8k, 1%, 1/8W, 0805 | 0805 | SMD | Bottom | 2 | 2
 |  | R7, R8 | 2 | 4.7k, 1%, 1/8W, 0805 | 0805 | SMD | Top | 2 | 4
 |  | R9 | 1 | 330R, 1%, 1/8W, 0805 | 0805 | SMD | Bottom | 2 | 2
 |  | R10, R11 | 2 | 330R, 1%, 1/8W, 0805 | 0805 | SMD | Top | 2 | 4
 |  | R12, R15, R16, R18, R19, R20 | 6 | 750R, 1%, 1/8W, 0805 | 0805 | SMD | Top | 2 | 12
 |  | R14 | 1 | 750R, 1%, 1/8W, 0805 | 0805 | SMD | Bottom | 2 | 2
Digikey | EG2531CT-ND | S1, S2 | 2 | TL3342 surface mount pushbutton | E-SWITCH-TL3342 | SMD | Top | 4 | 8
Digikey | CKN5005-ND | SW1 | 1 | Slide switch | PCB Switch | TH | Top | 5 | 5
 |  | U1 | 2 | 1x7 female socket | HDR1x7 | TH | Top | 7 | 14 | Two rows of female sockets to accept a breakout board
STMicroelectronics | TSC888AILT | U2 | 1 | TSC888 Curent Sense Amplifier | SOT23-5 | SMD | Bottom | 5 | 5
Microchip | ATMEGA644PA-AU | U3 | 1 | 8-bit AVR Microcontroller, 64KB Flash, 2KB EEPROM, 4KB SRAM | 44TQFP | SMD | Top | 44 | 44
Murata | OKL-T/3-W12P-C | VR1 | 1 | DC DC Convertor | OKL-T/3-W12 | SMD | Top | 12 | 12
Microchip | MCP1825S-3302E/DB | VR2 | 1 | 3V3 Voltage Regulator | SOT233-4N | SMD | Bottom | 4 | 4
Digikey | SER3629CT-ND | X1 | 1 | Epson 20MHz crystal | XTAL TSX3225 | SMD | Top | 4 | 4

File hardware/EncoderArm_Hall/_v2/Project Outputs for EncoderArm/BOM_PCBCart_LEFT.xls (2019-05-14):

Manufacturer | Manufacturer Part Number | Designator | Qty | Description | Case | SMD ,BGA,LCC,OR TH | Top/Bottom | points | Total points | Comment
 |  | R2 | 1 | 10k, 1%, 1/8W, 0805 | 0805 | SMD | Top | 2 | 2
 |  | R3 | 1 | 10k, 1%, 1/8W, 0805 | 0805 | SMD | Bottom | 2 | 2
 |  | P1 | 1 | 2x3 female socket | HDR2x3 | TH | Top | 6 | 6 | Socket on same side as SL1, SL2
Allegro | A1120ELHLT-T | SL1, SL2 | 2 | A1120 Hall effect sensor | SOT23W | SMD | Top | 3 | 6
Allegro | A1120ELHLT-T | SR1, SR2 | 0 |  |  |  |  |  |  | DO NOT FIT

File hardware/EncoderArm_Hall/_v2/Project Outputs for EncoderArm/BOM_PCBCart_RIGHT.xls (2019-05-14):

Manufacturer | Manufacturer Part Number | Designator | Qty | Description | Case | SMD ,BGA,LCC,OR TH | Top/Bottom | points | Total points | Comment
 |  | R2 | 1 | 10k, 1%, 1/8W, 0805 | 0805 | SMD | Top | 2 | 2
 |  | R3 | 1 | 10k, 1%, 1/8W, 0805 | 0805 | SMD | Bottom | 2 | 2
 |  | P1 | 1 | 2x3 female socket | HDR2x3 | TH | Bottom | 6 | 6 | Socket on same side as SR1, SR2
Allegro | A1120ELHLT-T | SL1, SL2 |  |  |  |  |  |  |  | DO NOT FIT
Allegro | A1120ELHLT-T | SR1, SR2 | 2 | A1120 Hall effect sensor | SOT23W | SMD | Top | 3 | 6

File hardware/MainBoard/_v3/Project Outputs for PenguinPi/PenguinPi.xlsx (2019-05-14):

Comment | Description | Designator | Footprint | LibRef | Quantity | Value | Supplier
CAP SMD | Surface mount capacitor | C1, C2, C5, C6, C7, C8, C9, C10, C11, C12 | CAPC2012X07N | CAP SMD | 10 | 10uF, 10uF, 100nF, 100nF, 100nF, 9pF, 9pF, 100nF, 100nF, 100nF
Cap | Capacitor | C3 | 6-0805_M | Cap | 1 | 1uF
Cap Pol1 | Polarized Capacitor (Radial) | C4 | 6-0805_M | Cap Pol1 | 1 | 4u7
SMD DIODE | Surface mount Diode | D1 | SODFL470X110-2N | SMD DIODE | 1 |  | Digikey 1727-5317-1-ND
DC Jack SMD |  | DC1 | DC Jack SMD | DC Jack SMD | 1
RGEF250 | PPTC Thermal Fuse | F1 | MF-MSMF250/16X-2 | RGEF250 | 1 |  | E14 2519587
INDUCTOR SMD | Surface Mount Inductor - varying sizes | L1 | CM322522 | INDUCTOR SMD | 1 | 10uH | E14 9357866
LED RGB RightAngle |  | LED1 | LED RGB RightAngle | LED RGB RightAngle | 1
 |  | LED2, LED3, LED4 | LED YELLOW RightAngle | LED Yellow RightAngle | 3
PWR |  | LED5 | LED YELLOW RightAngle | LED Yellow RightAngle | 1
Header 3X2 | Header, 3-Pin, Dual row | LEFT, RIGHT | HDR2X3 | Header 3X2 | 2
XT30 |  | P2 | XT30 - PCB mount | XT30 | 1
Charger |  | P3 | Molex SL70553 2 way | Molex SL 70553 2way | 1 |  | E14 2060691
HAT | Header, 8-Pin, Dual row | P4 | HDR2X8 | Header 8X2 | 1
ISP | 3 by 2 header, staggered pin arrangement | P5 | Header 3x2 nonstandard | Header 3x2 Staggered | 1
RPi Header | GPIO connector for Raspberry Pi Microcomputer | PI | RPI 2 Header | RPi 2 Header | 1
RES SMD | 0805 surface mount resistor | R1 | RESC3216X06M | RES SMD | 1 | 0.05R
RES SMD | 0805 surface mount resistor | R2, R3, R4, R5, R6, R7, R8, R9, R10, R11, R12, R13, R14, R15, R16, R17, R18 | RESC2012X07N | RES SMD | 17 | 10k, 1.34k, 27k, 10k, 6.8k, 4.7k, 4.7k, 330R, 325R, 325R, 750R, 10k, 750R, 750R, 750R, 10k, 750R
SDN | TL 3342 surface mount pushbutton | S1 | E-SWITCH-TL3342 | E-SWITCH-PUSHBUTTON | 1 |  | Digikey EG2531CT-ND
RST | TL 3342 surface mount pushbutton | S2 | E-SWITCH-TL3342 | E-SWITCH-PUSHBUTTON | 1
PCB Switch |  | SW1 | PCB Switch | PCB Switch | 1 |  | Digikey CKN5005-ND
DRV8835_CARRIER | DRV8835 Motor Controller | U1 | DRV8835_CARRIER | DRV8835_CARRIER | 1
TSC888 | Curent Sense Amplifier | U2 | SOT95P280X145-5N | TSC888 | 1
ATmega644PA-AU | 8-bit AVR Microcontroller, 64KB Flash, 2KB EEPROM, 4KB SRAM, 44-pin TQFP, Industrial Grade (-40°C to 85°C) | U3 | 44A_L | CMP-0095-00289-2 | 1
Murata OKL-T/3-W12 |  | VR1 | OKL-T/3-W12 | Murata OKL-T/3-W12 | 1
FT_SOT223 |  | VR2 | SOT233-4N | FT_SOT223 | 1
20MHz |  | X1 | XTAL TSX3225 | XTAL ABM3B | 1 |  | Digikey 535-9125-2-ND

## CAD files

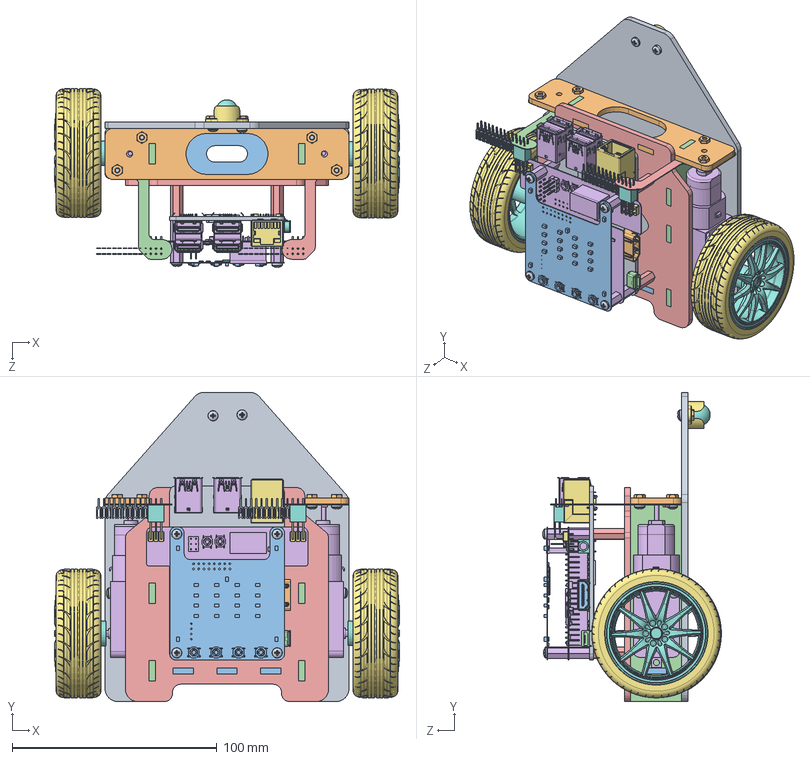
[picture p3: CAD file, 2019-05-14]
hardware/SBDef2 with wheels and PCBs V3.SLDASM
168.4 x 151.0 x 87.3 mm
SBDef Bottom
SBDef Front
SBDef Back
SBDef Side x 2
SBDef Top
SBDefMotorModel x 2
Tire x 2
Rim x 2
carte_mere
HDMI_socket_cover
HDMI_socket_inside
HDMI_socket_large_pin x 10
HDMI_socket_small_pin x 9
usb3x2 x 2
RJ45_10P_TJ3009
PCB_Stereo_Jack_(body)
PCB_Stereo_Jack_(GND_contact)
PCB_Stereo_Jack_(channel_contact_2)
PCB_Stereo_Jack_(channel_contact_1)
USB
Standoff 15mm x 4
Standoff 10mm x 8
My ScaledCaster
My scaled Ball
pan cross head_am x 18
hex nut style 1_am x 6
HAT_ID01_OLED
EncoderArm1 Left
EncoderArm1Right
PenguinPi_1A
Header 2P - Right Angle - Jameco x 6
pin x 52

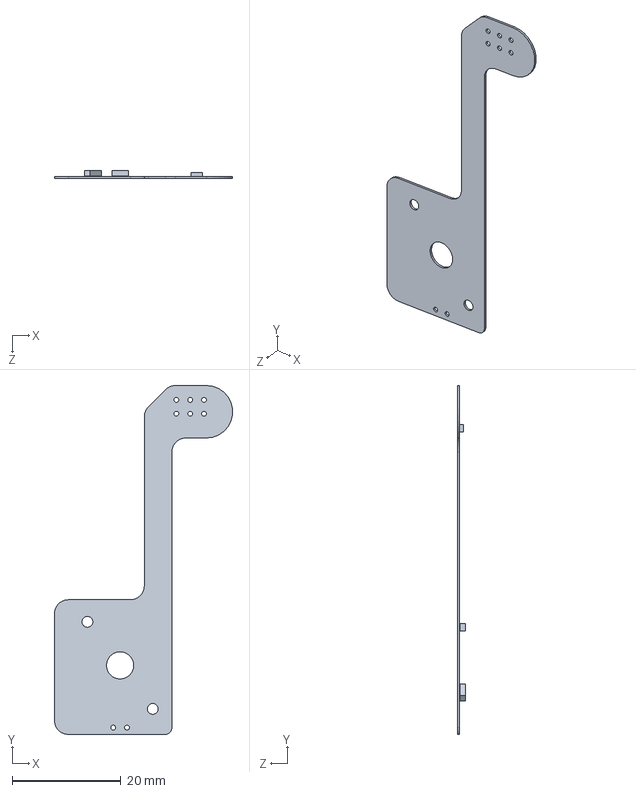
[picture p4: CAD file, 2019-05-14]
hardware/EncoderArm_Hall/_v2/EncoderArm1Right.SLDPRT
32.7 x 64.1 x 1.51 mm

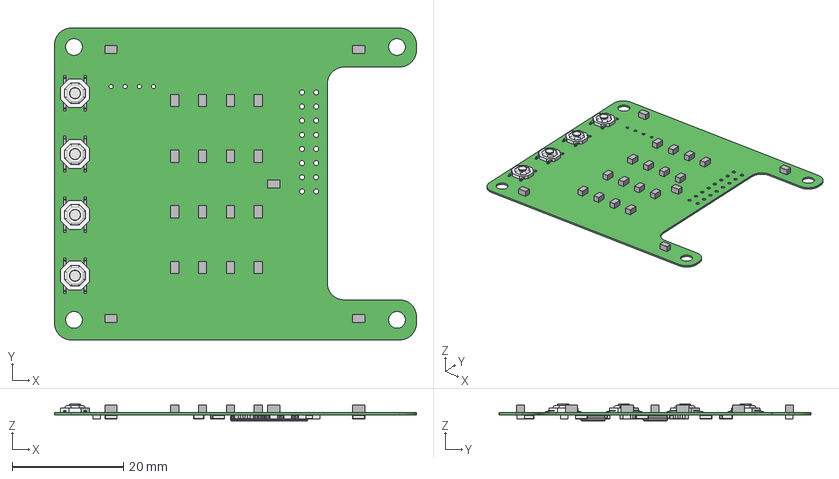
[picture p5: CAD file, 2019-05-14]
hardware/HAT_ID01_OLED/HAT_ID01_OLED.step
65.0 x 56.0 x 3.05 mm
Board
Mid_Body x 17
Open_CASCADE_STEP_translator_6.8_16.2.1 x 34
Mark x 17
Extruded x 21
Open_CASCADE_STEP_translator_6.8_34.1.1 x 4
mark x 4
Open_CASCADE_STEP_translator_6.8_34.3.1 x 8
Open_CASCADE_STEP_translator_6.8_34.5.1 x 8
Open_CASCADE_STEP_translator_6.8_34.7.1 x 16
Open_CASCADE_STEP_translator_6.8_13.1 x 2
Open_CASCADE_STEP_translator_6.8_13.2.1 x 2
Leader x 48
E-SWITCH-TL3342 x 4

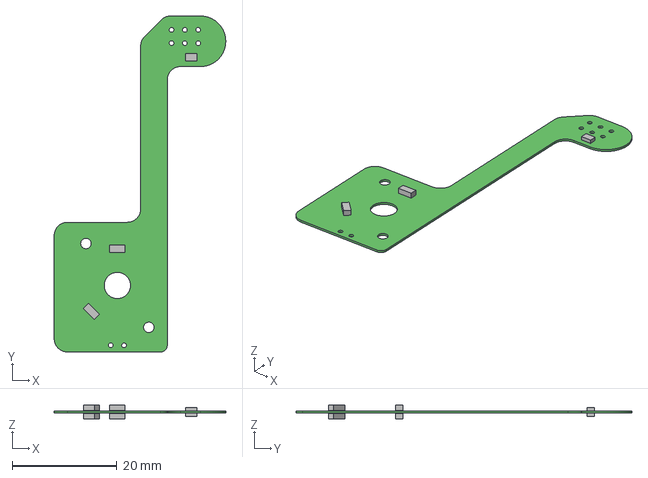
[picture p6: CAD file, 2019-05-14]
hardware/EncoderArm_Hall/_v2/EncoderArm.step
32.8 x 64.1 x 2.61 mm
Board
Extruded x 6

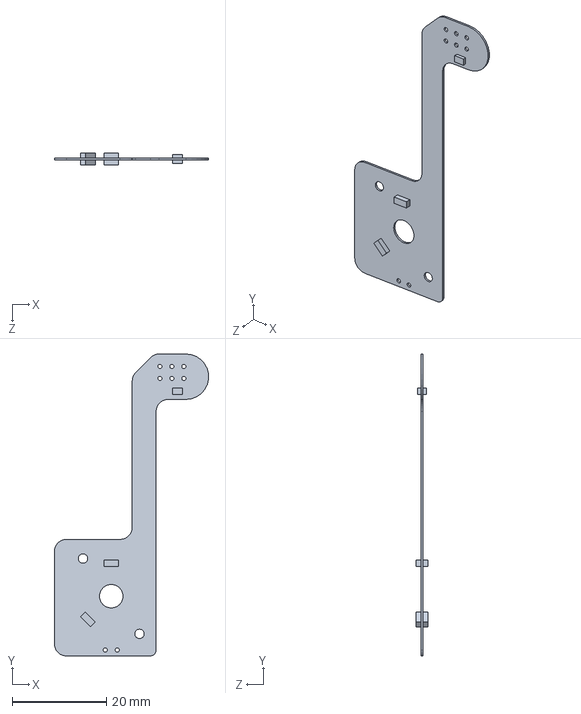
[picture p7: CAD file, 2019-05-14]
hardware/EncoderArm_Hall/_v2/EncoderArm1.SLDPRT
32.7 x 64.1 x 2.61 mm

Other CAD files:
hardware/EncoderArm_Hall/_v2/EncoderArm1 Left.SLDPRT

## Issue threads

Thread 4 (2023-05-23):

Default camera resolution maxes out CPUs

BotBitz, 2023-05-23:
When running at 1640 x 1232 camera resolution ppweb.py maxes out all 4 cores of the Rpi3B+.

Proposed solution is to reduce the stock camera resolution for the script to 640 x 480 resulting much lower CPU usage. See below.
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

Tobias-Fischer, 2023-05-23:
Hi @BotBitz - I tried 640x480 at first. However, this resulted in a cropped image that did not show the full field of view. I think this needs a bit of playing around with the new picamera2 library to properly get sorted out. Agreed though that we should reduce the resolution to save CPU.

Tobias-Fischer, 2023-05-23:
Relevant:
- https://github.com/raspberrypi/picamera2/issues/450
- https://github.com/raspberrypi/picamera2/discussions/585
- `ScalerCrop` in https://datasheets.raspberrypi.com/camera/picamera2-manual.pdf

BotBitz, 2023-05-23:
Agreed. I made some quick patches to see what I could get going and it
looked cropped but haven’t had enough time to play yet. Will get a PR once
I have something working.

On Wed, 24 May 2023 at 7:20 am, Tobias Fischer ***@***.***>
wrote:

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

Tobias-Fischer, 2023-07-17:
Fixed in #5

Closed 2023-07-17.

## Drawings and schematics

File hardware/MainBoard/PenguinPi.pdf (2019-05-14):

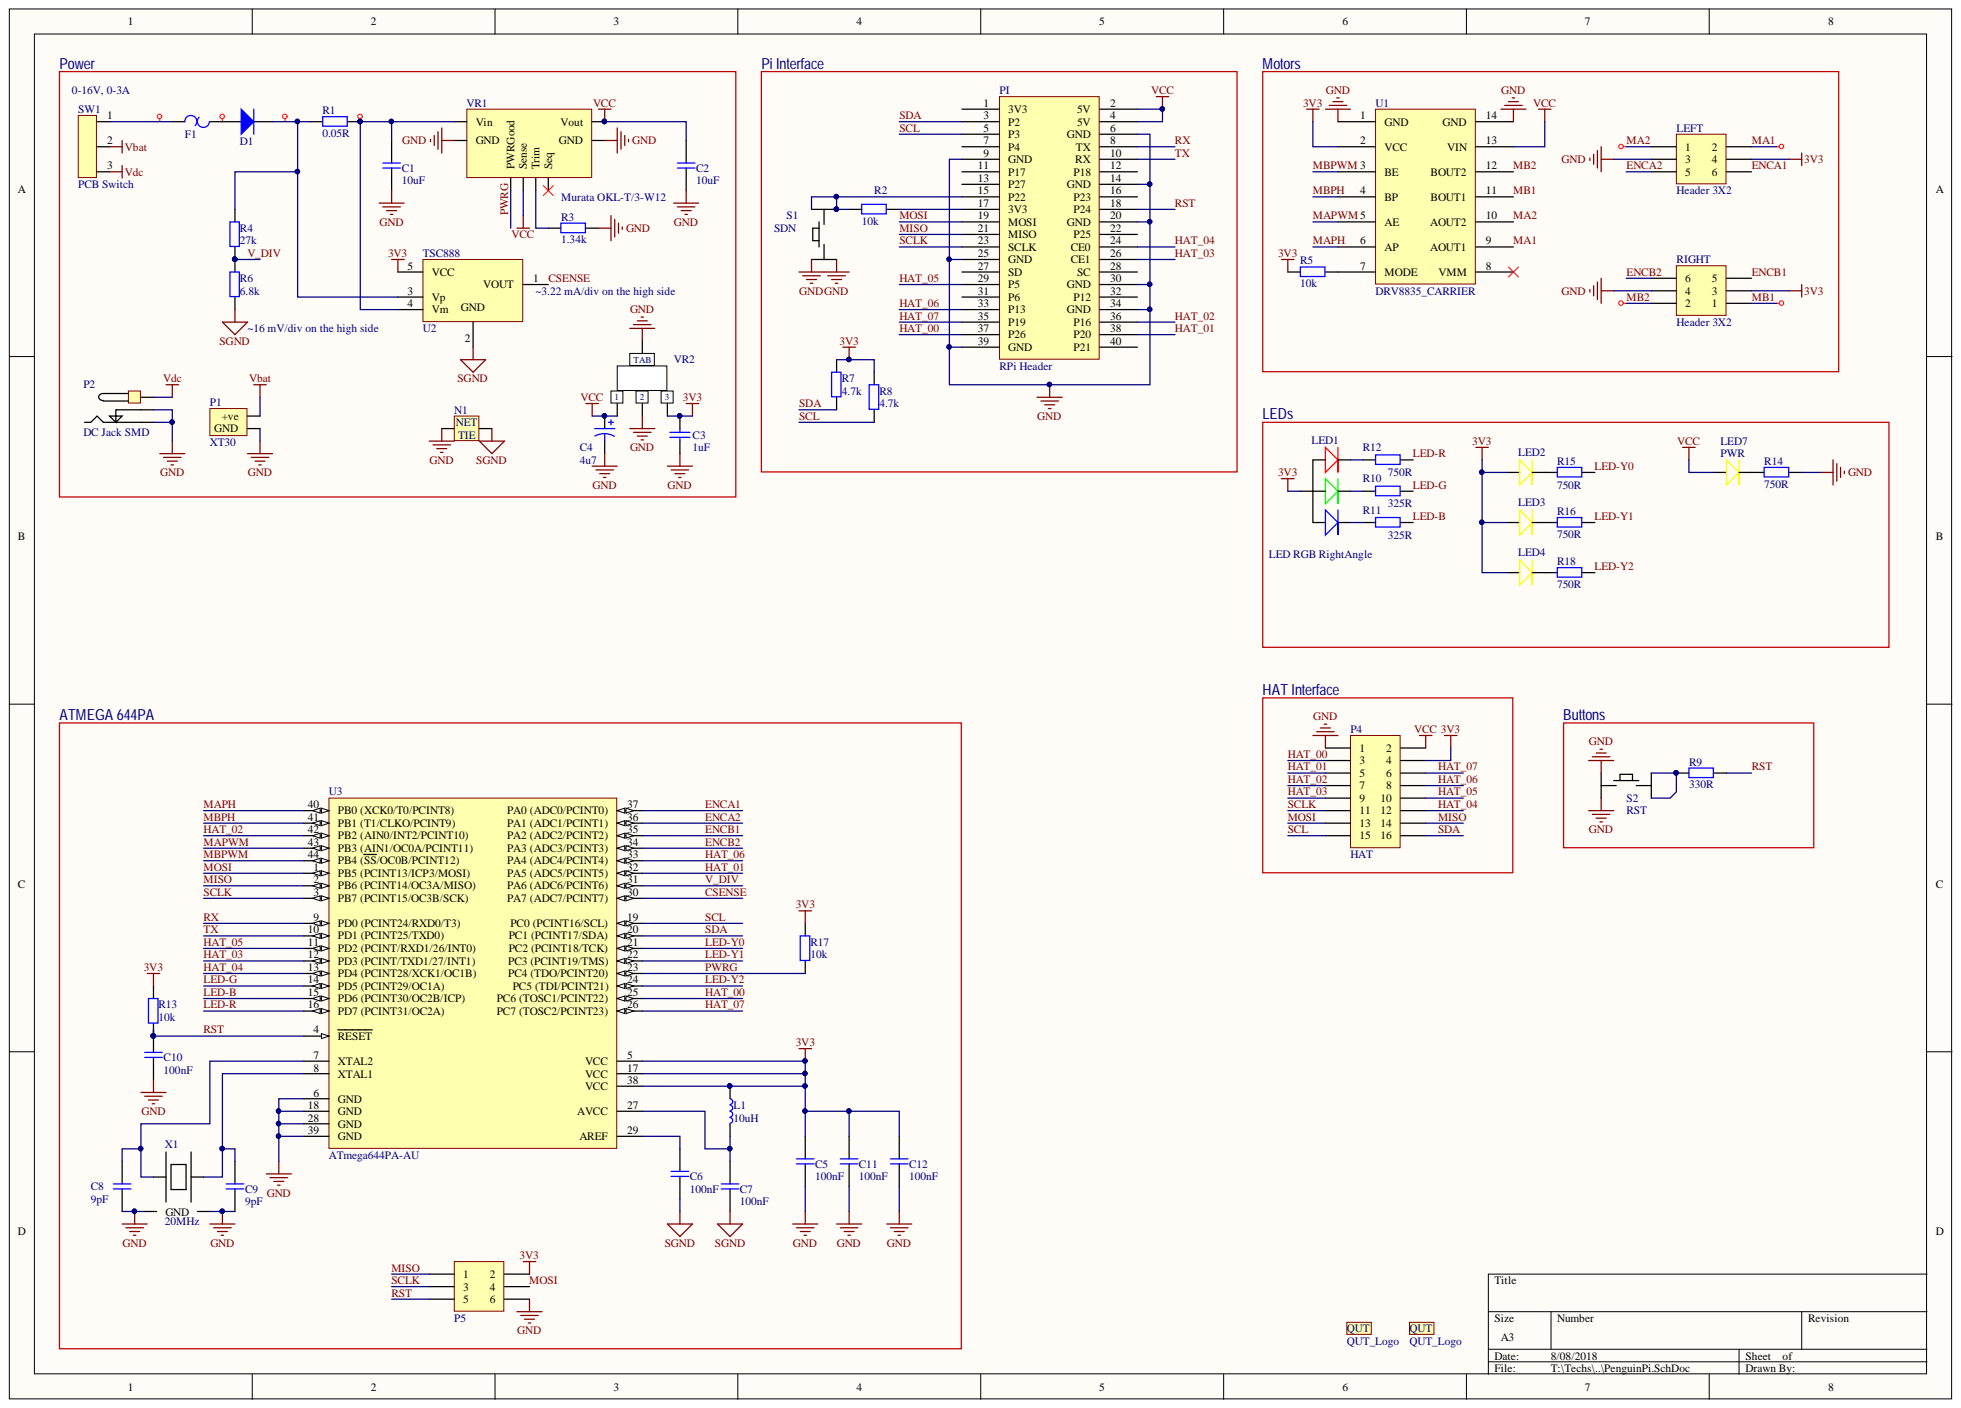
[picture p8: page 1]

CSENSE
~3.22 mA/div on the high side

~16 mV/div on the high side
SGND

GND 6

GND 28

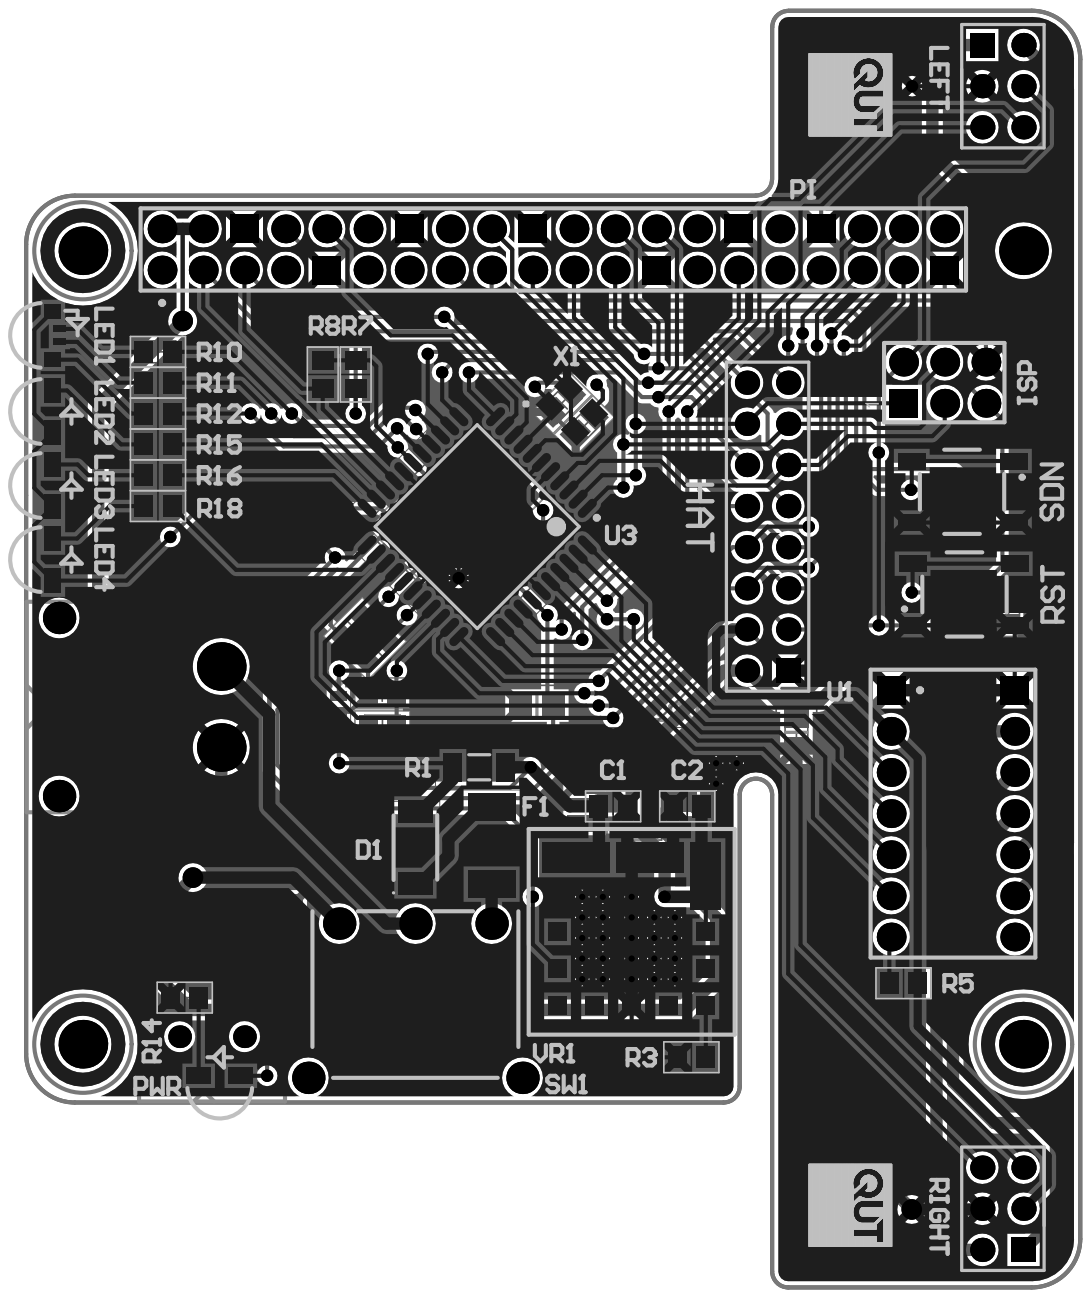
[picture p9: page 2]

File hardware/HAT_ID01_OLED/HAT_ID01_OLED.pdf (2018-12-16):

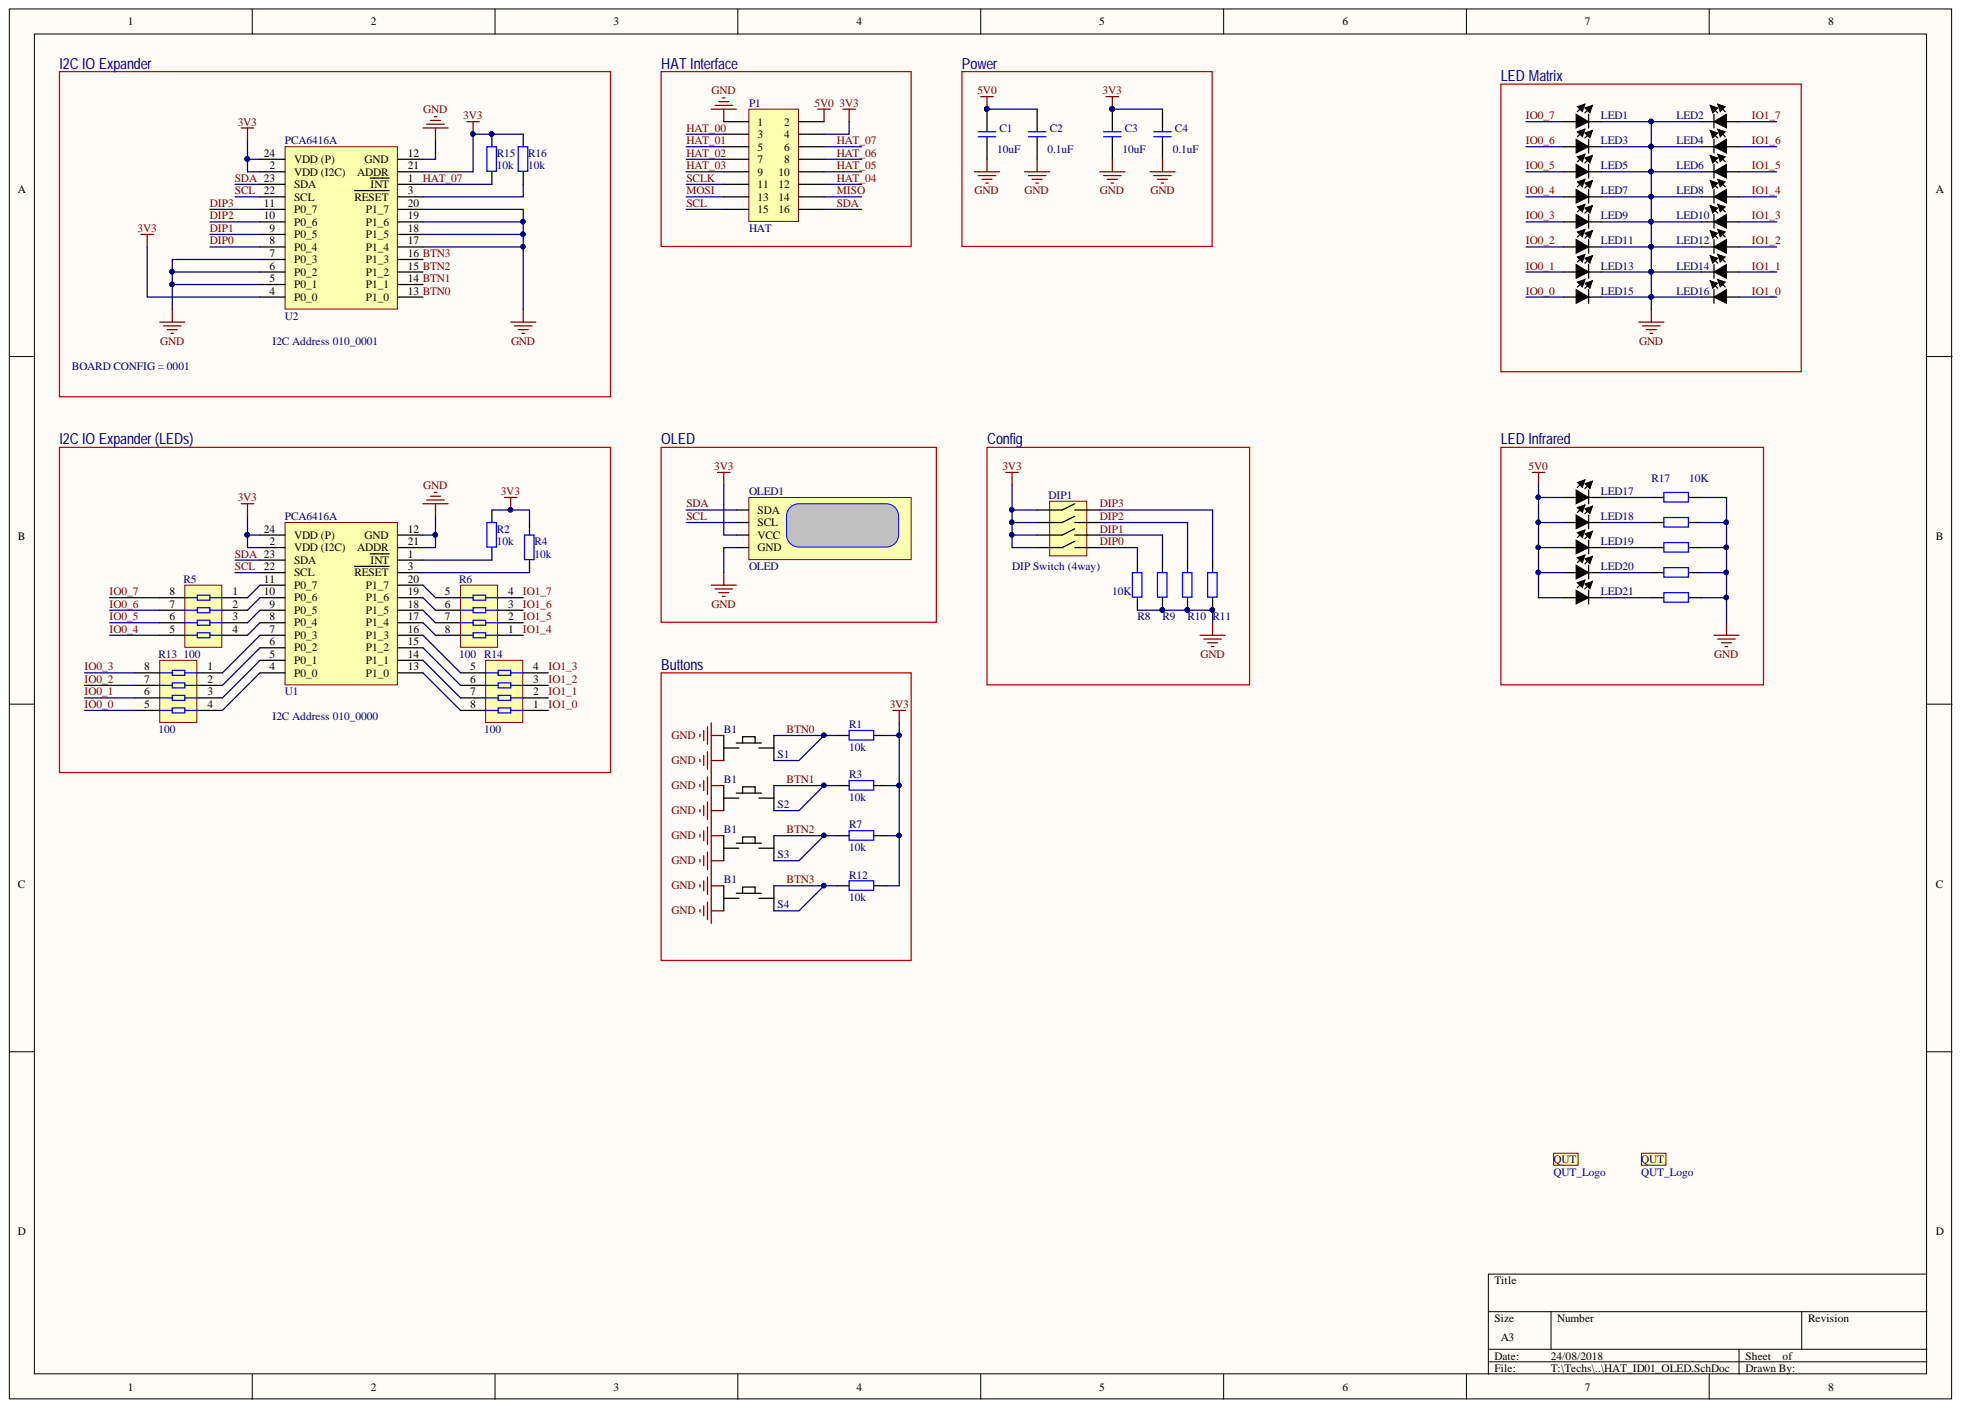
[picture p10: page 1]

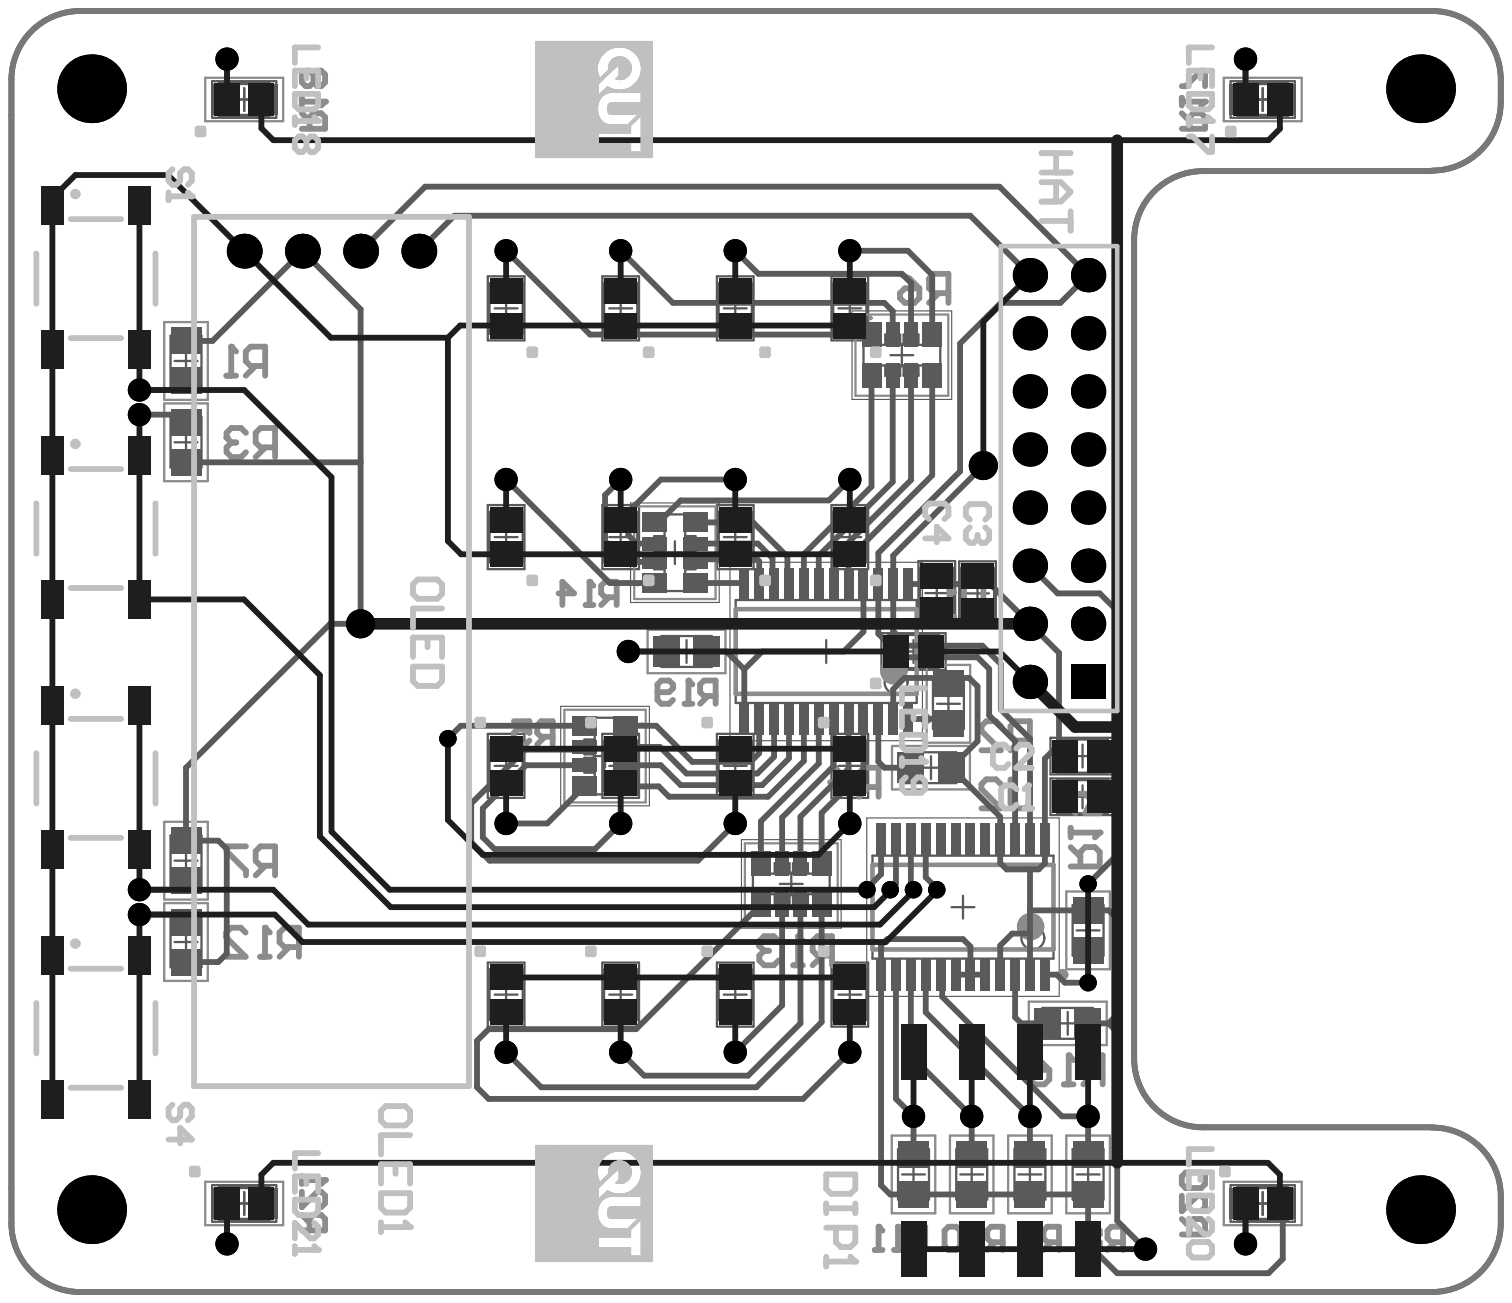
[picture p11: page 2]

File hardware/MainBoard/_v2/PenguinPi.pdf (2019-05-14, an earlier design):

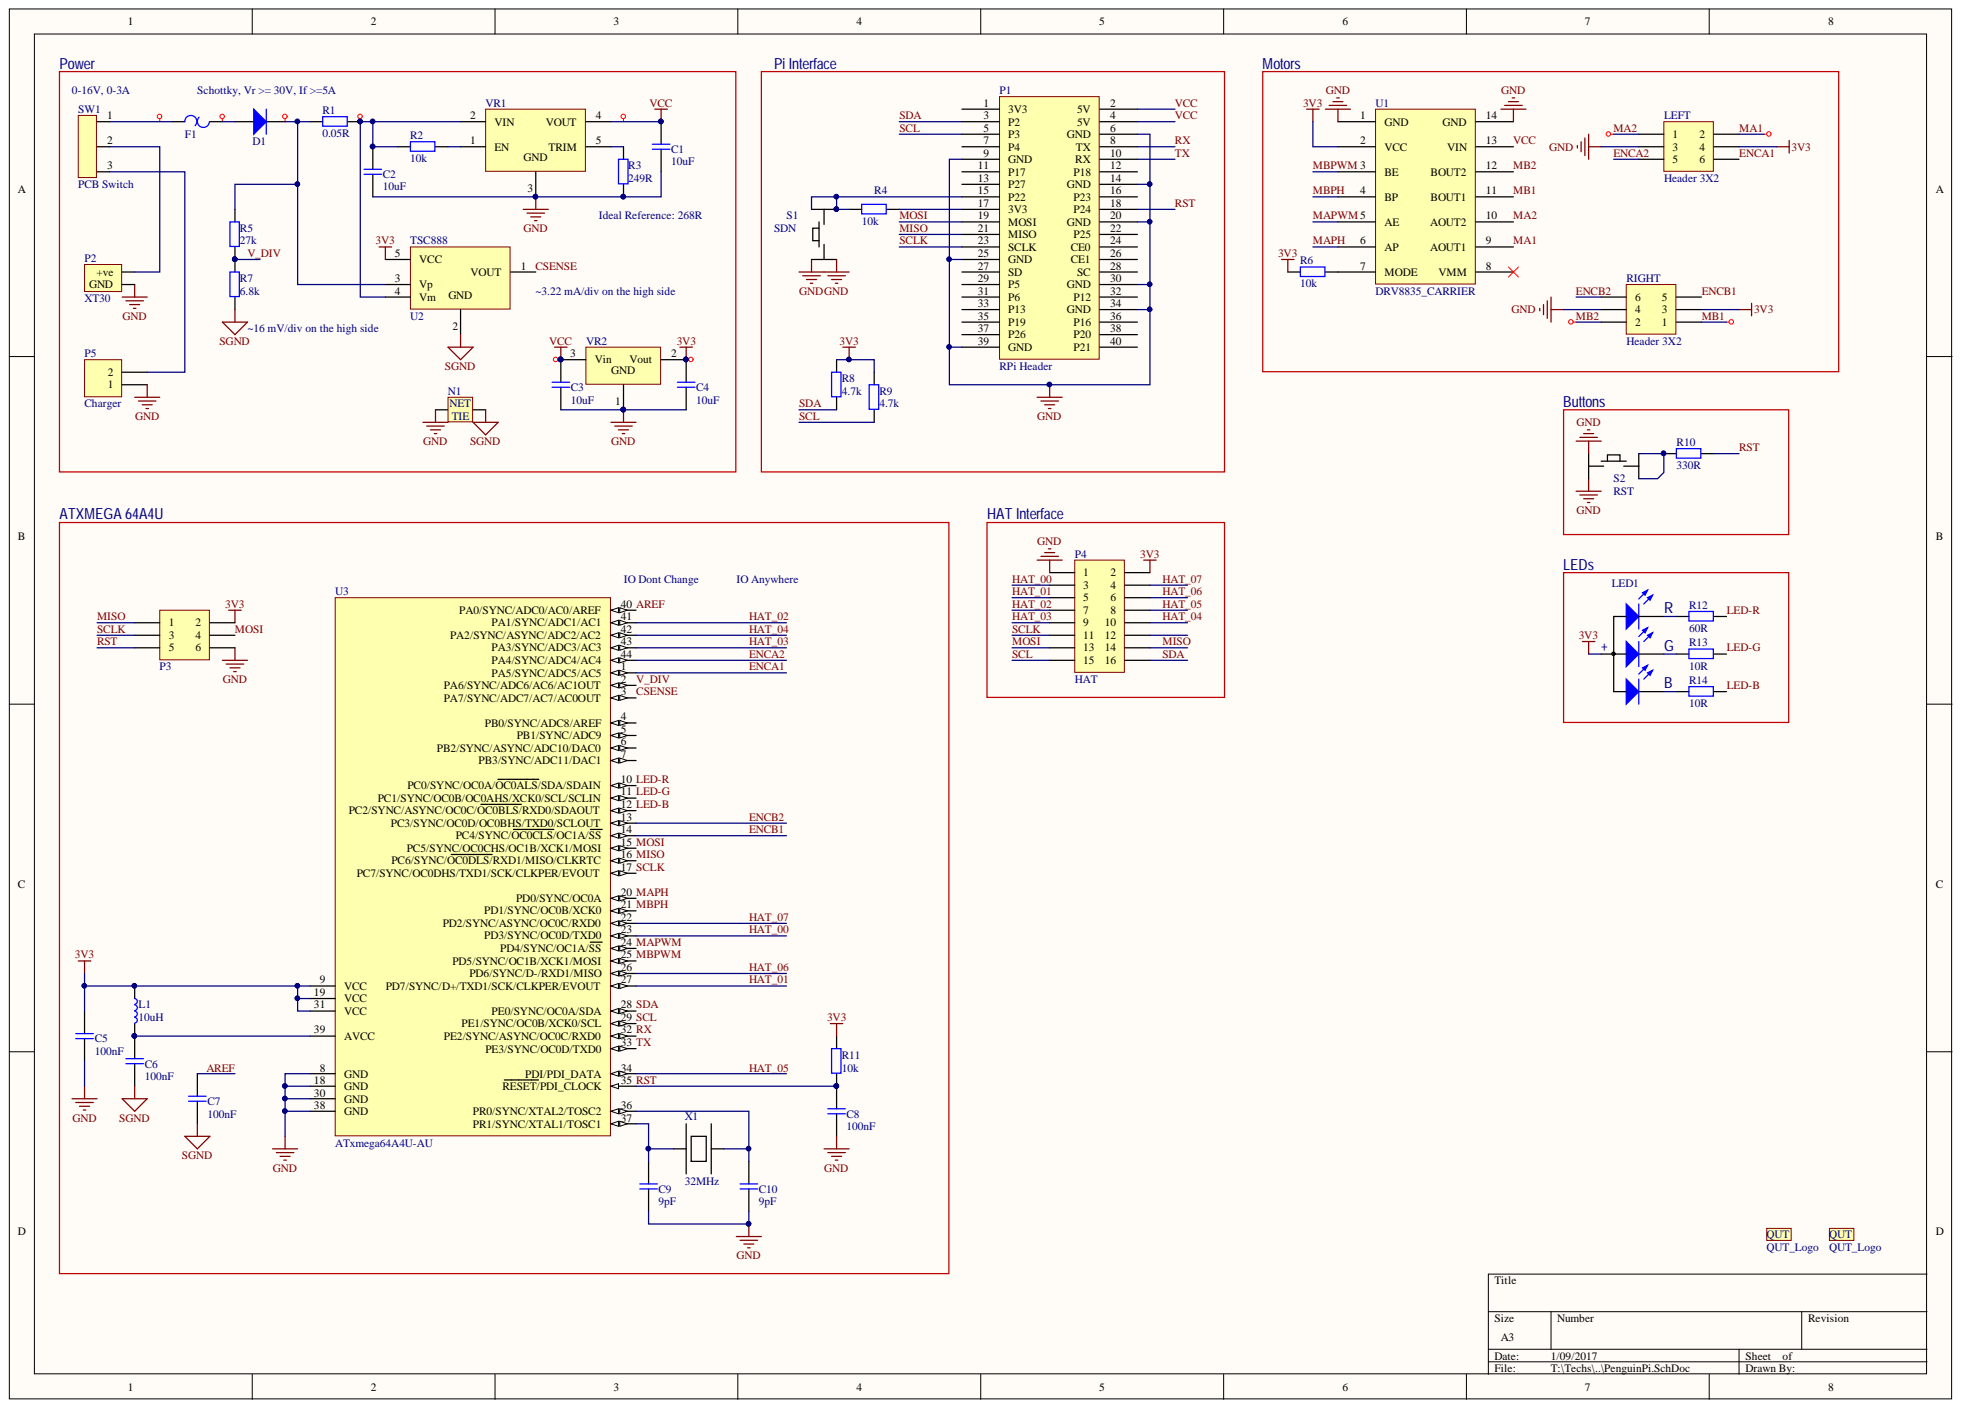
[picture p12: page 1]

A/div on the high s

V/div on the high s

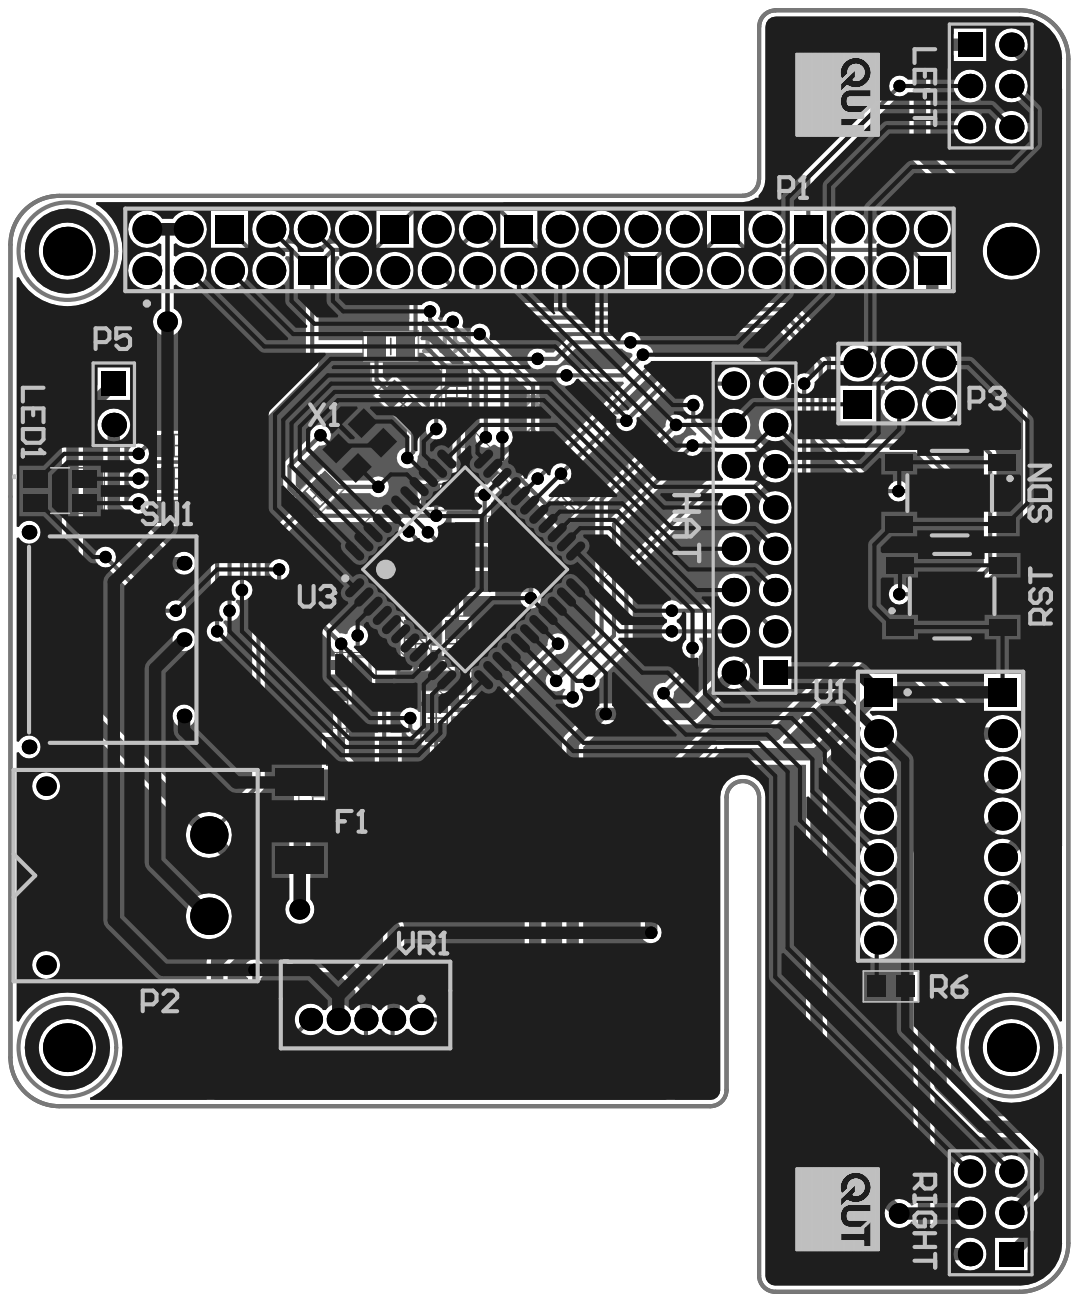
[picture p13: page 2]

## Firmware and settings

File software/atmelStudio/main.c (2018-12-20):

/*
 * main.c
 *
 * NOTES
 * ========
 *
 * Motor, set_power() invokes MOTOR_SET_velocity_dPS which sets motor->dir and motor->setSpeedDPS
 * set_degrees() invokes MOTOR_SET_DEGREES which sets motor->setDegrees which is the PID setpoint
 *
 * LED usage:
 *  red 	- valid command packet
 *  green 	- encoder ISR
 *  blue 	- bad command or framing error
 */

/*
 * cpu is ATmega644PA
 */
#define DEBUG 0 

#include <stdlib.h>
#include <stdio.h>
#include <string.h>
#include <stdarg.h>
#include <math.h>

#include <avr/interrupt.h>
#include <util/delay.h>
#include <avr/io.h>
#include <util/crc16.h>
#include <util/atomic.h>

#include "i2cmaster.h"
#include "uart.h"

#include "global.h"
#include "hat.h"
#include "datagram.h"
#include "motor.h"
#include "timer.h"

// parameters
#define ERRMSGLEN   80

#define BATTERY_WARNING  7000
#define BATTERY_SHUTDOWN  6500

const uint8_t   control_interval = 20; // ms
const uint8_t   adc_interval = 10; // ms
const uint8_t   oled_interval = 200; // ms


// global variables
Motor 		motorR;
Motor 		motorL;
LED         leds[6];
AnalogIn 	vdiv;
AnalogIn 	csense;
Performance performance;

uint8_t    pid_on = 3;  // PID control is on

volatile uint8_t  oled_update_now = 0;
volatile uint8_t  second_now = 0;
volatile uint32_t seconds_counter;  // wraps every 18 hours

uint8_t  low_voltage = 0;
uint8_t  pishutdown_up = 0;


// forward defines
void test_leds();



//######################################################################
//
// ISRs
//
//######################################################################


// initialize the counters so they are not in sync
volatile uint8_t control_counter = 0;
volatile uint8_t adc_counter = 10;
volatile uint8_t oled_counter = 5;
volatile uint16_t milliseconds_counter = 12;

ISR( TIMER1_COMPA_vect ) {
    // period of 1ms

    // 1 second heartbeat on green LED
    if (++milliseconds_counter >= 1000) {
        milliseconds_counter = 0;
        seconds_counter++;
        second_now = 1;
    }

    // update all LED counters
    for (uint8_t i=0; i<NLEDS; i++) {
        if (leds[i].count > 0)
            if (--leds[i].count == 0)
                leds[i].state = 0;      // flag this LED to be turned off now
    }

    // initiate an OLED update in the main loop
    if (++oled_counter >= oled_interval) {
        oled_counter = 0;
        oled_update_now = 1;
    }

    // initiate ADC conversion
    if (++adc_counter > adc_interval) {
        adc_counter = 0;

        ADMUX = ADC_REF | vdiv.channel;    // select volts
		ADCSRA |= (1<<ADSC);            // start conversion
    }

    // time for motor control?
    if (++control_counter < control_interval)
        return;

    control_counter = 0;
    if (pid_on == 0)
        return;

    // do motor control now

    // enable interrupts and carry on
    sei();  
   
    // Calculate motor speed control
    motor_velocity_control(&motorR);
    motor_velocity_control(&motorL);

    // Set the PWM values
    OCR0A = mapRanges( abs(motorR.command), 0, 100, 0, 255 );
    OCR0B = mapRanges( abs(motorL.command), 0, 100, 0, 255 );

    // Set motor driver polarities
    if (motorR.command >= 0)
        PORTB &= ~(1<<MOTOR_A_PHA); 
    else if (motorR.command < 0)
        PORTB |= (1<<MOTOR_A_PHA); 

    if (motorL.command >= 0)
        PORTB &= ~(1<<MOTOR_B_PHA);
    else if (motorL.command < 0)
        PORTB |= (1<<MOTOR_B_PHA);
}

ISR( PCINT0_vect ) {
	//All encoders are now on one PCINT vector
	//Externally on PCINT{3:0} which is PA3:0

	//detect which pin triggered the interrupt
		uint8_t PINA_val   = PINA;
		uint8_t encA1 = ( PINA_val & (1<<MOTOR_A_ENC_1) )>>MOTOR_A_ENC_1; 	//store the current state
		uint8_t encB1 = ( PINA_val & (1<<MOTOR_A_ENC_2) )>>MOTOR_A_ENC_2;
		uint8_t encA2 = ( PINA_val & (1<<MOTOR_B_ENC_1) )>>MOTOR_B_ENC_1; 	//store the current state
		uint8_t encB2 = ( PINA_val & (1<<MOTOR_B_ENC_2) )>>MOTOR_B_ENC_2;
		
	//Update Motor states
		motor_encoder_update( &motorR, encA1, encB1 ); 
		motor_encoder_update( &motorL, encA2, encB2 ); 
	
	//Update LEDs
        LED_DEBUG_G(2);
}

uint16_t            adc[8];
volatile uint8_t   adc_done;

ISR( ADC_vect ) {
    // conversion complete, 42us after initiation

    uint8_t chan = ADMUX & 0x1f;    // which channel did we just read?

    adc[chan] = ADC;     // get the value and stash it


    if (chan == vdiv.channel) {
        // just read volts, ask for current
        ADMUX = ADC_REF | csense.channel;  // select current
        ADCSRA |= (1<<ADSC);            // start conversion
    } else
        adc_done = 1;
}


//#################################################################################################
//                      Main polling loop
//#################################################################################################


int
main(void)
{
    timer_t t0, tf;
	 
	init_structs();
	io_init();	
    // Set up velocity PID
    motor_init(&motorR, 0);
    motor_init(&motorL, 1);
	
	uart_puts_P("PenguinPi v2.0\n");
	detect_reset();	
	hat_init();
    test_leds();
    datagram_init();
	
    stats_init(&performance.loop_time);
    debugmessage("starting main loop");
    timer_get(&t0);
    while (1) 
    {
        // get timing stats for main loop
        timer_get(&tf);
        uint32_t dt = timer_diff_us(&tf, &t0);
        stats_add(&performance.loop_time, dt);
        /*
        if (dt > 2000) {
            debugmessage("dt = %lu", dt);
            debugmessage("%lu %u %u %lu %u %u", tf.sec, tf.ms, tf.clock, t0.sec, t0.ms, t0.clock);
        }
        */
        t0 = tf;

        // Check for a new datagram
        uint8_t c = datagram_poll();
        if (c)
            hat_usertext_add(c);
		
		//LED update
        for (uint8_t i=0; i<NLEDS; i++) {
            LED *led = &leds[i];

            if(led->state)
                LEDOn(i);
            else
                LEDOff(i);
        }

		//Analog update
        if (adc_done) {
            adc_done = 0;

            io_analog_filter_step(&vdiv, adc[6]);
            io_analog_filter_step(&csense, adc[7]);
        }

		if (vdiv.smooth < battery.mvolts_warning) {
            // battery volts are below warning level
            if (battery.warning == 0) {
                battery.warning = 1;
                oled_invert_display(1); // invert the display if not already done
            }

            if (vdiv.smooth < battery.mvolts_shutdown)
                hat_shutdown(" LOW VOLTAGE SHUTDOWN ");
		}

        if ((PINB & (1<<PB7)) == 0)
            LEDOff(Y4);
        else
            LEDOn(Y4);

        // has the RPi acknowledged a shutdown request?
        if ((PINB & (1<<PB7)) == 0) {
            // GPIO11 is low
            // EITHER shutdown daemon not running OR shutdown in progress
            if (pishutdown_up)  // daemon was running, must be shutdown
                hat_shutdown(" TURN RaspberryPI OFF SAFELY ");
        } else {
            // GPIO11 is high
            // shutdown daemon is running
            pishutdown_up = 1;
        }

        // Update the hat
        hat_update(&oled_update_now);
		
        if (pid_on == 0) {
            // no velocity control, command PWM directly
            OCR0A = mapRanges( abs(motorR.velocity_dmd), 0, 100, 0, 255 );
            OCR0B = mapRanges( abs(motorL.velocity_dmd), 0, 100, 0, 255 );
            
            // Set motor driver polarities
            if (motorR.command >= 0)
                PORTB &= ~(1<<MOTOR_A_PHA); 
            else if (motorR.command < 0)
                PORTB |= (1<<MOTOR_A_PHA); 

            if (motorL.command >= 0)
                PORTB &= ~(1<<MOTOR_B_PHA);
            else if (motorL.command < 0)
                PORTB |= (1<<MOTOR_B_PHA);
        }
        if (second_now) {
            second_now = 0;
            // debug message here
            //debugmessage("mean %lu max %lu", stats_mean(&performance.loop_time), performance.loop_time.max);
            if ((seconds_counter % 60) == 0) {
                stats_init(&performance.loop_time);
                performance.loop_time.max = 0;
                //debugmessage("reset stats");
            }
            if ((seconds_counter % 60) == 20) {
                //debugmessage("n=%lu, sx=%lu, sx2=%lu", performance.loop_time.n, performance.loop_time.sum, performance.loop_time.sum2);
                //debugmessage("mean=%lu, std=%lu, mx=%lu", 
                        //stats_mean(&performance.loop_time), stats_std(&performance.loop_time), performance.loop_time.max);
            }
        }
		
        //main_loop_debug();
    }
}

// central error message handler, sends to serial port and OLED
void errmessage(const char *fmt, ...)
{
    va_list ap;
    char    buf[ERRMSGLEN];

    va_start(ap, fmt);

    vsnprintf(buf, ERRMSGLEN, fmt, ap);
    uart_puts("ERR: ");
    uart_puts(buf);
    uart_puts("\n");

    hat_show_error(buf);

    va_end(ap);

    performance.errors++;
}

void debugmessage(const char *fmt, ...)
{
    va_list ap;
    char    buf[ERRMSGLEN];

    va_start(ap, fmt);

    vsnprintf(buf, ERRMSGLEN, fmt, ap);
    uart_puts("DBG: ");
    uart_puts(buf);
    uart_puts("\n");

    //hat_show_error( buf);

    va_end(ap);
}

//#################################################################################################
//
// INITs
//
//#################################################################################################

void init_structs(void){
	vdiv.scale 				= 16.018497;//mV per div
    vdiv.channel = 6;
    vdiv.alpha = 0.95;
	csense.scale 			= 3.2226562;//mA per div
    csense.channel = 7;
    csense.alpha = 0.95;
	
	battery.mvolts_warning = BATTERY_WARNING;
    battery.warning = 0;
    battery.mvolts_shutdown = BATTERY_SHUTDOWN;
	
    for (uint8_t i=0; i<NLEDS; i++) {
        leds[i].state = 0;
        leds[i].count = 0;
    }
	
}

void
test_leds()
{
    for (uint8_t i=0; i<NLEDS; i++) {
        LEDOn(i);
        _delay_ms(300);	
        LEDOff(i);
        _delay_ms(200);	
    }
}

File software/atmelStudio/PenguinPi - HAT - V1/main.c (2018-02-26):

/*
 * PenguinPi - HAT - V1.c
 *
 * Created: 19/09/2016 19:19:41
 * Author : Jack
 */ 

/*
 * NOTES
 * ========
 *
 * Motor, set_power() invokes MOTOR_SET_SPEED_DPS which sets motor->dir and motor->setSpeedDPS
 * set_degrees() invokes MOTOR_SET_DEGREES which sets motor->setDegrees which is the PID setpoint
 *
 * LED usage:
 *  red - valid command packet
 *  green - encoder ISR
 *  blue - bad command or framing error
 */

/*
 * cpu is ATmega 328PB
 */
#define BAUD 115200
#define F_CPU 12000000UL

#include <stdlib.h>
#include <avr/io.h>
#include <stdio.h>
#include <avr/interrupt.h>
#include <util/delay.h>
#include <math.h>
#include <util/crc16.h>
#include "i2cmaster.h"
#include "uart.h"
#include "PenguinPi.h"
#include "PCA6416A.h"


Motor motorA;
Motor motorB;
Servo servoA;
Servo servoB;
LED ledR;
LED ledG;
LED ledB;
Display displayA;
Button buttonA;
Button buttonB;
Button buttonC;
AnalogIn vdiv;
AnalogIn csense;

//Global variables
char fstring[32];
uint8_t datagramG[DGRAM_MAX_LENGTH+1];
int8_t mAQuadTable[4][4] = {{ 0, +1, -1,  2},
							{-1,  0,  2, +1},
							{+1,  2,  0, -1},
							{ 2, -1, +1,  0}};

int8_t mBQuadTable[4][4] = {{ 0, -1, +1,  2},
							{+1,  0,  2, -1},
							{-1,  2,  0, +1},
							{ 2, +1, -1,  0}};
//digit strings for display: includes hexadecimal only
uint8_t digit0[] = {DIGIT0_0, DIGIT0_1, DIGIT0_2, DIGIT0_3, DIGIT0_4, DIGIT0_5, DIGIT0_6, DIGIT0_7, DIGIT0_8, DIGIT0_9, DIGIT0_A, DIGIT0_B, DIGIT0_C, DIGIT0_D, DIGIT0_E, DIGIT0_F};
uint8_t digit1[] = {DIGIT1_0, DIGIT1_1, DIGIT1_2, DIGIT1_3, DIGIT1_4, DIGIT1_5, DIGIT1_6, DIGIT1_7, DIGIT1_8, DIGIT1_9, DIGIT1_A, DIGIT1_B, DIGIT1_C, DIGIT1_D, DIGIT1_E, DIGIT1_F};
//Battery struct
struct Battery {
	float cutoff;//volts
	uint16_t count;
	uint16_t limit;//number of cycles until it triggers a shutdown
} battery;

ISR(PCINT1_vect){
	//Motor A encoders
	//detect which pin triggered the interrupt
	uint8_t enc1val = (PINC & (1<<MOTOR_A_ENC_1))>>MOTOR_A_ENC_1; //store the current state
	uint8_t enc2val = (PINC & (1<<MOTOR_A_ENC_2))>>MOTOR_A_ENC_2;
	
	if(motorA.encoderMode == 0){
		//single encoder mode, on pin 1
		//uint8_t encdiff = motorA.enc1PinState ^ enc1val;
		if(motorA.enc1PinState ^ enc1val){
			if(motorA.dir == 1){
				motorA.position++;
				motorA.lastDir = 1;
			}else if(motorA.dir == -1){
				motorA.position--;
				motorA.lastDir = -1;
			}else{
				//wheel slip!!
				//probably going to still be rotating in the direction it just was, so use that past value
				if(motorA.lastDir == 1) motorA.position++;
				else if(motorA.lastDir == -1) motorA.position--;
			}
			motorA.enc1PinState = enc1val;
		}//otherwise there was a tick but it wasn't the first channel...

	}else if(motorA.encoderMode == 1){
		//standard quadrature
		uint8_t lastEncSum = (motorA.enc1PinState<<1)|(motorA.enc2PinState);
		uint8_t encSum = (enc1val<<1)|(enc2val);
		int8_t effect = mAQuadTable[lastEncSum][encSum];

		motorA.position += effect;

		motorA.enc1PinState = enc1val;
		motorA.enc2PinState = enc2val;

	}else if(motorA.encoderMode == 2){
		//x4 counting (xor'ed both channels)
		uint8_t x4 = enc1val ^ enc2val;
		if(motorA.enc1PinState ^ x4){
			if(motorA.dir == 1){
				motorA.position++;
				motorA.lastDir = 1;
			}else if(motorA.dir == -1){
				motorA.position--;
				motorA.lastDir = -1;
			}else{
				//wheel slip!!
				//probably going to still be rotating in the direction it just was, so use that past value
				if(motorA.lastDir == 1) motorA.position++;
				else if(motorA.lastDir == -1) motorA.position--;
			}
			motorA.enc1PinState = x4;
		}
	}else{
		//my mode isn't specified
		motorA.encoderMode = 1;//set to default
	}

	ledG.state = 1;
	ledG.count = 100;
}

ISR(PCINT3_vect){
	//Motor B encoders
	//detect which pin triggered the interrupt
	uint8_t enc1val = (PINE & (1<<MOTOR_B_ENC_1))>>MOTOR_B_ENC_1; //store the current state
	uint8_t enc2val = (PINE & (1<<MOTOR_B_ENC_2))>>MOTOR_B_ENC_2;
	
	if(motorB.encoderMode == 0){
		//single encoder mode, on pin 1
		//uint8_t encdiff = motorB.enc1PinState ^ enc1val;
		if(motorB.enc1PinState ^ enc1val){
			if(motorB.dir == 1){
				motorB.position++;
				motorB.lastDir = 1;
			}else if(motorB.dir == -1){
				motorB.position--;
				motorB.lastDir = -1;
			}else{
				//wheel slip!!
				//probably going to still be rotating in the direction it just was, so use that past value
				if(motorB.lastDir == 1) motorB.position++;
				else if(motorB.lastDir == -1) motorB.position--;
			}
			motorB.enc1PinState = enc1val;
		}//otherwise there was a tick but it wasn't the first channel...

	}else if(motorB.encoderMode == 1){
		//standard quadrature
		uint8_t lastEncSum = (motorB.enc1PinState<<1)|(motorB.enc2PinState);
		uint8_t encSum = (enc1val<<1)|(enc2val);
		int8_t effect = mBQuadTable[lastEncSum][encSum];

		motorB.position += effect;

		motorB.enc1PinState = enc1val;
		motorB.enc2PinState = enc2val;

	}else if(motorB.encoderMode == 2){
		//x4 counting (xor'ed both channels)
		uint8_t x4 = enc1val ^ enc2val;
		if(motorB.enc1PinState ^ x4){
			if(motorB.dir == 1){
				motorB.position++;
				motorB.lastDir = 1;
			}else if(motorB.dir == -1){
				motorB.position--;
				motorB.lastDir = -1;
			}else{
				//wheel slip!!
				//probably going to still be rotating in the direction it just was, so use that past value
				if(motorB.lastDir == 1) motorB.position++;
				else if(motorB.lastDir == -1) motorB.position--;
			}
			motorB.enc1PinState = x4;
		}
	}else{
		//my mode isn't specified
		motorB.encoderMode = 1;//set to default
	}

	ledG.state = 1;
	ledG.count = 100;
}

ISR(PCINT0_vect){
	uint8_t btnAval = (PINB & (1<<BTN_A))>>BTN_A;

	buttonLogic(&buttonA, btnAval);
}

ISR(PCINT2_vect){
	//determine which button triggered the interrupt
	uint8_t btnBval = (PIND & (1<<BTN_B))>>BTN_B;
	uint8_t btnCval = (PIND & (1<<BTN_C))>>BTN_C;

	if(buttonB.pinState ^ btnBval){//has it actually changed?
		buttonLogic(&buttonB, btnBval);
	}
	if(buttonC.pinState ^ btnCval){
		buttonLogic(&buttonC, btnCval);
	}
}

ISR(TIMER2_OVF_vect){//period of 21.3333us. use a counter for longer delays
	static uint8_t motorControlCount = 0;
	
	if(motorControlCount < CONTROL_COUNT){//should achieve a period of 64 us
		motorControlCount++;
	}else{
		//set PID flags
		motorA.pidTimerFlag = 1;
		motorB.pidTimerFlag = 1;
		motorControlCount = 0;
	}
	
	if(ledR.count > 0) ledR.count--;
	else ledR.state = 0;
	if(ledG.count > 0) ledG.count--;
	else ledG.state = 0;
	if(ledB.count > 0) ledB.count--;
	else ledB.state = 0;
	
	if(buttonA.debounceCount > 0) buttonA.debounceCount--;
	if(buttonB.debounceCount > 0) buttonB.debounceCount--;
	if(buttonC.debounceCount > 0) buttonC.debounceCount--;
}
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

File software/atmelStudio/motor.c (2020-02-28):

#include "motor.h"
#include "global.h"
#include    <util/atomic.h>

void
motor_velocity_control(Motor *motor)
{
    // Scale the set point to match the non-pid commands
    // motor control interval is 20ms
    // setpoint after scaling is the number of ticks per time step (of the loop)
    int16_t vdmd = motor->velocity_dmd/5;
    int16_t motor_pos;

    // estimate velocity (encs/interval)
    ATOMIC_BLOCK(ATOMIC_FORCEON) {
        motor_pos = motor->position;
    }
    motor->velocity = motor_pos - motor->position_prev;
    motor->position_prev = motor_pos;

    // Error
    motor->verror = vdmd - motor->velocity;

    // Error integral
    if (motor->Kvi > 0)
        motor->verrorsum += motor->verror;
    else
        motor->verrorsum = 0;

    // clip the integral
    if (motor->verrorsum > 100)
        motor->verrorsum = 100;
    else if (motor->verrorsum < -100)
        motor->verrorsum = -100;

    // PI velocity controller
    motor->command = motor->Kvp * motor->verror +
                     motor->Kvi * motor->verrorsum;

    /*
    debugmessage("sp %d, dt %d, e %d, u %d, mc0 %d, mc %d", 
        setPoint, deltaDegrees, pid->error, pid->output, mc0, pid->command);
        */

    // Clip the commands
    if (motor->command > 100)
        motor->command = 100;
    else if (motor->command < -100)
        motor->command = -100;

#ifdef notdef
    // If the input is 0, reset the controller
    if (setPoint == 0) {
        motor->command = 0;
        motor->error = 0;
        motor->error_prev = 0;
    }
#endif
}

void
motor_init(Motor *motor, uint8_t id)
{
    motor->command = 0;
    motor->velocity = 0;
    motor->verror = 0;
    motor->velocity_dmd = 0;
    motor->verrorsum = 0;
    motor->Kvp = 0;
    motor->Kvi = 1;
    motor->id = id;
    motor->encoderMode = 1;
}

// PIC: not sure I believe this approach, just sample B on an A edge...
// encoder state transition lookup tables
static int8_t 	mAQuadTable[4][4] = {{ 0, +1, -1,  2},
							 {-1,  0,  2, +1},
							 {+1,  2,  0, -1},
							 { 2, -1, +1,  0}};

static int8_t  mBQuadTable[4][4] = {{ 0, -1, +1,  2},
							 {+1,  0,  2, -1},
							 {-1,  2,  0, +1},
							 { 2, +1, -1,  0}};

void 
motor_encoder_update( Motor *motor, uint8_t encA, uint8_t encB )
{
	
    switch(motor->encoderMode) {
        case 0: //single encoder mode, on pin 1
            if ( motor->encA_prev ^ encA ){
                if( motor->command > 0){
                    motor->position++;
                }else if( motor->command < 0 ){
                    motor->position--;
                }
                motor->encA_prev = encA;
            }
            break;

        case 1: { //standard quadrature
            uint8_t lastEncSum 	= (motor->encA_prev<<1)|(motor->encB_prev);
            uint8_t encSum 		= (encA<<1)|(encB);
            int8_t  effect;
            
            if ( motor->id == 1 ) {
                //Motor B
                effect 			= mBQuadTable[lastEncSum][encSum];
            }
            else {
                //Motor A
                effect 			= mAQuadTable[lastEncSum][encSum];
            }
            
            motor->position 	+= effect;
        
            motor->encA_prev = encA;
            motor->encB_prev = encB;
            break;
        }
#ifdef notdef
        case 2: { //x4 counting (xor'ed both channels)
            uint8_t x4 = enc_1_val ^ enc_2_val;
            if(motor->enc1PinState ^ x4){
                if(motor->dir == 1){
                    motor->position++;
                    motor->lastDir = 1;
                }else if(motor->dir == -1){
                    motor->position--;
                    motor->lastDir = -1;
                }else{
                    //wheel slip!!
                    //probably going to still be rotating in the direction it just was, so use that past value
                    if(motor->lastDir == 1) 		motor->position++;
                    else if(motor->lastDir == -1) 	motor->position--;
                }
                motor->enc1PinState = x4;
            }
        }
#endif
    }
}

#ifdef notdef
void fn_dbg_motor ( Motor *motor ){
	char 	fstring[32];
	
	if ( motor->dir == -1 ) 	uart_puts_P("  dir: -1\n");
	else if ( motor->dir == 1 )	uart_puts_P("  dir:  1\n");
	else 						uart_puts_P("  dir:  0\n");					
	
	sprintf(fstring, "  enc: %6d\n", motor->position);
	uart_puts(fstring);
	uart_puts(fstring);
	uart_puts(fstring);			
	sprintf(fstring, "  dps: %6d\n", motor->velocity_dmd);
	uart_puts(fstring);		
	
}
#endif
#ifdef notdef
int16_t 
motor_position_control(int16_t setPoint, Motor *motor)
{
	//based upon Application Note AVR221
	int16_t error = setPoint - motor->degrees;

	int16_t pTerm, dTerm;
	int32_t iTerm;
	
	//P term, also limit overflow
	if(error > motor->maxError)			pTerm = INT16_MAX;
	else if(error < -motor->maxError)	pTerm = -INT16_MAX;
	else								pTerm = motor->gainP * error;
	
	//I term, also limit overflow
	int32_t newSum = motor->errorSum + error;
	if(newSum > motor->maxErrorSum){
		motor->errorSum = motor->maxErrorSum;
		iTerm = INT32_MAX/2;
	}else if(newSum < -motor->maxErrorSum){
		motor->errorSum = -motor->maxErrorSum;
		iTerm = -(INT32_MAX/2);
	}else{
		motor->errorSum = newSum;
		iTerm = motor->gainI * motor->errorSum;
	}

	//D term //put this on a slower interval
	dTerm = motor->gainD * (motor->lastVal - motor->degrees);
	
	motor->lastVal = motor->degrees;
	
	int32_t result = (pTerm + iTerm + dTerm)/PID_SCALE;
	
	if(result > INT16_MAX) result = INT16_MAX;
	else if(result < -INT16_MAX) result = -INT16_MAX;
	
	return (int16_t)result;		
}
#endif

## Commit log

2018-02-27 IP found in motor server heartbeat
2018-07-25 Revert "test commit"
    This reverts commit 4727bdda59b02e27ecb9c727b332beeb73480a68.
    [penguinPi.py]
2018-07-26 Improvements to serial packet read code. Look for ASCII non-packet data and send that to stdout, useful for error messages originating on the Atmel.
    [penguinPi.py]
2018-07-26 Improve all error messages, context and details, and systematically use a macro - errmessage() - to format and send them.
    [main.c]
2018-07-26 A micro webserver using flask. It provides human-readable web pages as well as web GET/POST for programmatic access to robot and camera data.
2018-08-15 Systematic change of all error messages to errmessage() which sends to console and OLED
    [main.c]
2018-08-16 added to the union to allow 2xuint16 in a message (not sure the union is that useful) added commands for 4 lines of user text on the OLED added commands to get DIP, and set/get motorspeed/encoder cha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
2018-08-16 declare debug message function made a boot time pattern on the blue LED array, not all on tidy up OLED screen sequencing, add the error screen
2018-08-16 added macros for debug LEDs, can all be disabled in single spot, all errors are now red LEDs added declare and definition for debugmessage(), like errmessage(), but different prefix change storage of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
    fiddle with boot time LED sequences
    exclude big chunks of unwanted code with #ifdef notdef, rather than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
    [main.c]
2018-08-16 add more detail for pages, eg. OS and hardware level, encoders, voltages etc. change mA, mB to mLeft and mRight, clearer code added motor trapezoidal trajectory added web methods for reset, stop retu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
    [ppweb.py]
2018-08-16 add support for long datatype in datagram methods to get DIP switch, set/get motor/encoder
2018-08-16 remove Python version checking, it fails on syntax error with python 2 so this code never reached add error checking and diagnostics for malformed packets return encoder as unsigned int
    [penguinPi.py]
2018-08-17 major rewrite of datagram code and serial data logic added serial port exclusive locking, requires pyserial 3.4 the comms mutex is now used in a with construct getting the start byte is now within a 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
2018-08-17 Added new timing instrumentation. Moved control code to interrupt handler (ints reenabled)
2018-09-06 Big changes to LEDS: *time in ms * remove brightness * an array with enum * all 6 supported now
    changed to millisecond timer using timer 1
    * greatly reduced computation burden, easier time units to think about
    cf 12.8us
    * simple subtimers for motor, OLED refresh, ADC, lays groundwork for 100Hz ADC sampling
    formatting
    moved UI specific code to hat.[ch]
2018-09-06 screens are defined by enums remove old IP address representation, now its an array refresh now paced by flag set by millisecond interrupt handler gave oled_string printf like semantics, eliminate se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
2018-09-07 Update time structure
    now contains: seconds, milliseconds, 20MHz counter
2018-09-07 refactor
    Move crc and checkbuffer in from lib/PenguinPi.c
    Move address/opcode definitions from lib/PenguinPi.h to datagram.h, and
    change #defines to enums. These are parsed by defines.py to create a
    pickle file used by penguinPi.py
    rename exported functions as datagram_
    rename formatdatagram as datagram_return, use varargs to pass different
    types intead
    of union
    add longjmp to get back from errors deep in datagram processing
    replace lots of datagram checking code with datagram_validate function
    remove all references to degrees, remove unneeded opcode functions
    [datagram.c, datagram.h]
2018-09-07 refactor and tidy
    moved motor code from lib/PenguinPi to motor.c, consolidate motor state
    and control parameters into motor struct, general tidyup
    added analog filter and periodic sampling from TC1 ISR
    added millisecond and second counter to TC1 ISR
    changed motor names from A/B to R/L
    updated battery warning logic
    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
2018-09-07 refactor and reformat
    fixed bug with screen refresh logic
    moved Hat_oled define to hat.h
    removed MOTORS and POSITION screens
    reformat definitions
    removed old display logic from lowvolt shutdown
    finally removed IP setting per byte code, now a single uint32
    [hat.c]
2018-09-07 rewrite for robustness
    add GET_BUTTON opcode, should be for hat not oled
    datagram_poll returns the character, for use in text display
    renamed old serial i/o funcs as serial_getchar/waitchar/send
    rewrite the datagram detect logic
    poll the UART rather than relying on a single wait then poll, which
    might miss a late
    character
    better error handling and set/longjmp
    check datagram length at outset
    flash led, save datagram only on success
    tidy up error messages
    update performance stats
    [datagram.c, datagram.h]
2018-09-07 track changes in other modules
    update datagram polling logic
    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
2018-09-07 updates to OLED display and screen specific buttons
    change datastructure for error messages
    make button2 have screen specific functions
    - encoder clear, error msg clear, user msg clear
    tidy up text display on OLED, including button labels
    button 3 is user accessible
    DIP 2 controls display of L-shaped blue beacon
    scroll user text
    use inverse text for screen headings
    add inverse option for oled_string/character
    [hat.c]
2018-09-07 servo comands to enum add new ALL opcodes
2018-09-07 remove cruft fix bug with LED count set fix bug with negative speed for ALL_GET_ENC_SET_SPEED added ALL_GET_BUTTON reset previous position whenever zeroing position
    [datagram.c]
2018-09-07 Add user button code and declaratins add last datagram display screen for OLED prevent writing outside bounds of screen
    [hat.c]
2018-09-07 track changes to method names and semantics remove user level mutex, now done by penguinPi add logging
2018-09-10 elimination of PidController structs, all merged into Motor structs - eliminated separate direction variable, keep speeds as signed rejig of ADC code, now has regular sampling interval and 1st order 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
    general tidyup, remove cruft and old commented out code
    remove or comment out code to do with Mark 1 board display and buttons
    move lots of comms definitions, all datagram definitions, to datagram.h
    CRC and uart functions to datagram.c
    declare errormessage and debugmessage functions with attribute printf.
    [main.c]
2018-11-13 fix bug in regexp, symbols can contain digits printed alpha sorted list of all symbols
    [defines.py]
2018-11-13 on first step of digital filter initialize smooth value from current value
2018-11-13 change speed to velocity in motor structure names
2018-11-13 add thin space between numbers and units add battery current and picamera revision to the display add tooltips to the test buttons
2018-11-13 tidy up declarations at top of file change speed to velocity initialize alpha for digital filters
2018-11-13 change hat_lowvolts to hat_shutdown chnage speed to velocity hat_datagram handles new HAT_XXX commands support to set/get LED array, set screen, get user button
2018-11-13 macros to reference datagram payload added AD_MULTI object to handle both motors AD_ALL commands becomes AD_HAT or AD_MULTI commands remote AD_OLED, now part of AD_HAT object change SPEED to VEL add 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
2018-11-13 changed CRC polynomial to 0x97 use exclusive flag for serial if version >= 3.3 move some global functions to methods of Multi or Hat objects change speed to velocity remove old PID gain set/get, addi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
    [penguinPi.py]
2018-11-13 add funky code to get active interfaces without using popen add thread to set IP address, no need for separate process add command line arguments control interval of heartbeat and pose estimator thre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
2018-12-12 Fix the code that tests serialpy version, works if second number > 9
    [penguinPi.py]
2018-12-14 Change URLs in <img> tag to /camera/get to match new consistent naming convention implemented by server
2019-01-10 Missing self arg to all methods for Multi class
    [penguinPi.py]
2019-01-10 Add URLs for reset of encoder and estimated pose Make pose estimator robust to encoder reset Add support for thread safe pose reset
    [ppweb.py]
2019-01-10 Added support for printing to user text screen
2019-01-13 Add primitives to write text to PPI with mutex protection Remove version test for PySerial Add comments to motor speed control
2019-01-13 Added methods to write text to OLED Make the LiveScript uptodate, example of creating arrows on the LED array
2019-01-20 Working version. Camera image is converted to grey scale.
2019-01-21 Add a rule to set the fuses
2019-01-21 Add info about fuses
2019-05-14 Add hardware design
    [BOM_PCBCart.xls, BOM_PCBCart_LEFT.xls, BOM_PCBCart_RIGHT.xls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]
2019-12-09 Reinstate quadrature encoder mode Add clipping for integral term
2020-02-21 Add estimated velocity display to the encoder screen
2020-02-21 Remove race condition in velocity estimation.
2023-01-19 Add sample script to read image from web server
2023-03-10 IP camera offline instructions
2023-05-17 Add fixed focus for PiCameraV3
    [ppweb.py]
